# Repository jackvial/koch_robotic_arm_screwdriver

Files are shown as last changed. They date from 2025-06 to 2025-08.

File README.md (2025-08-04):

# Koch Robotic Arm Screwdriver

A screwdriver attachment and camera mount for the Koch robotic arm.

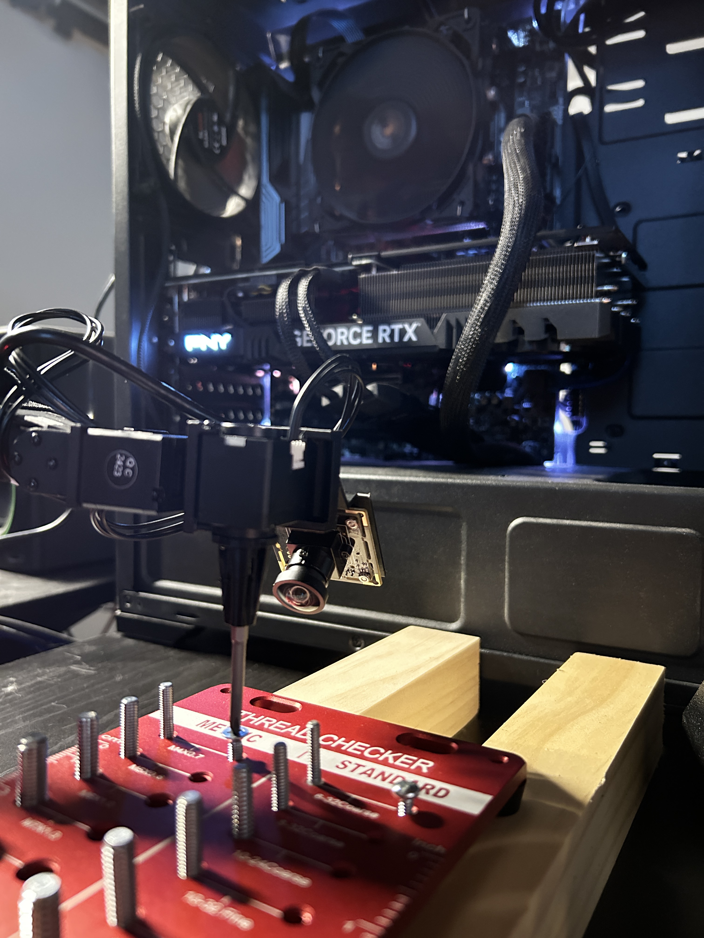
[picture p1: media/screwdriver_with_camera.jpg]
Screwdriver with camera


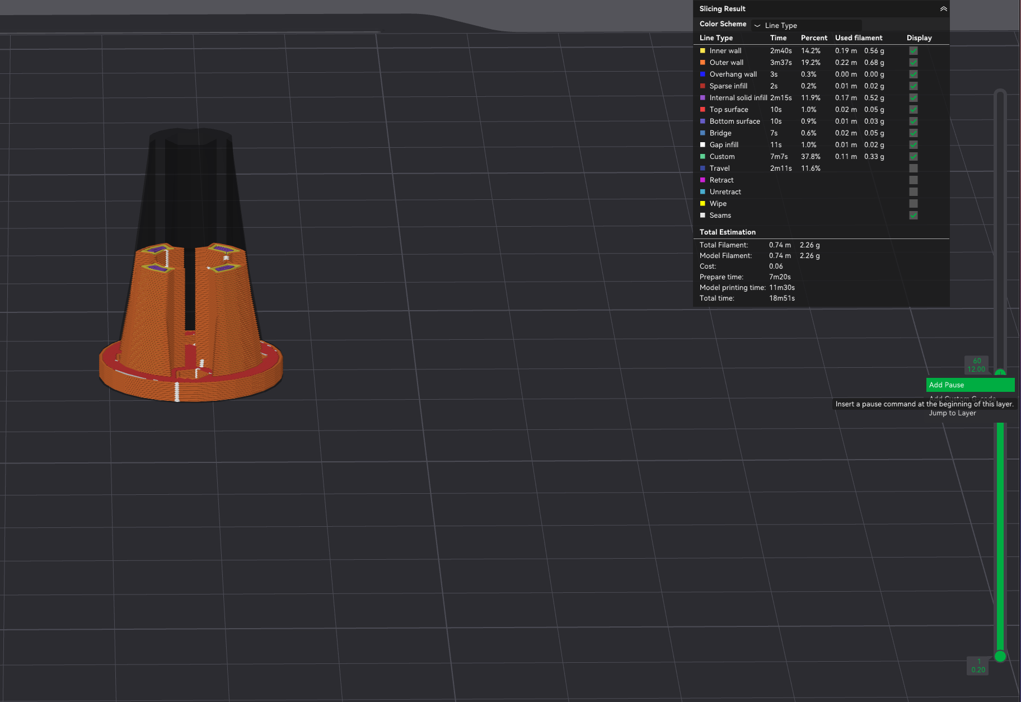
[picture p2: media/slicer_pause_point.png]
Slicer pause point


## Video Demo
[Watch the demo on YouTube](https://www.youtube.com/shorts/0c0qmF34xng)

## Screwdriver Bill of Materials
* SVPRO 5MP 30FPS USB Camera 
    * $53.99 on [Amazon](https://www.amazon.com/dp/B0D8SS2KNZ?ref_=ppx_hzod_image_dt_b_fed_asin_title_0_0&th=1)
* 6 mm diameter × 2 mm height neodymium magnets — 5 pcs  
    * $5.99 for 50 on [Amazon](https://www.amazon.com/dp/B079FLRQJP?ref=ppx_yo2ov_dt_b_fed_asin_title&th=1)*
* M2 8mm screws - I used this set
    * [Amazon](https://a.co/d/1YjSOn4)
* Precision screwdriver with standard 4mm hex shank bits - I am using the bits from this screwdriver
    * [Amazon](https://a.co/d/cEVycXf)

## Screwdriver Instructions
1. Position both parts on the print bed:  
   • `stl/screwdriver_servo_holder_with_camera_mount_v1.2.stl`  
   • `stl/koch_screwdriver_chuck.stl`
2. In your slicer (e.g. Bamboo Studio for the X1-Carbon) add a pause at the top of the magnet cavity.  
   See this tutorial: https://www.youtube.com/watch?v=SBewgnA0Z2s
3. When the print pauses, insert a stack of 5 magnets into the cavity.
4. Resume printing.

## Test Bed Bill of Materials
- 3 M4 hex nuts. I used the ones from this set on [Amazon](https://www.amazon.com/dp/B0CNY3BSXX?ref_=ppx_hzod_title_dt_b_fed_asin_title_0_0)
- 1 M4 8mm height flat head philips screw

## Test Bed Instructions
1. Position both parts on the print bed:  
   • `stl/test_bed.stl`
2. In the slicer, add a pause at the top of the nut cavities
3. When the print pauses, insert the 3 M4 hex nuts into the nut cavities.
4. Resume printing.

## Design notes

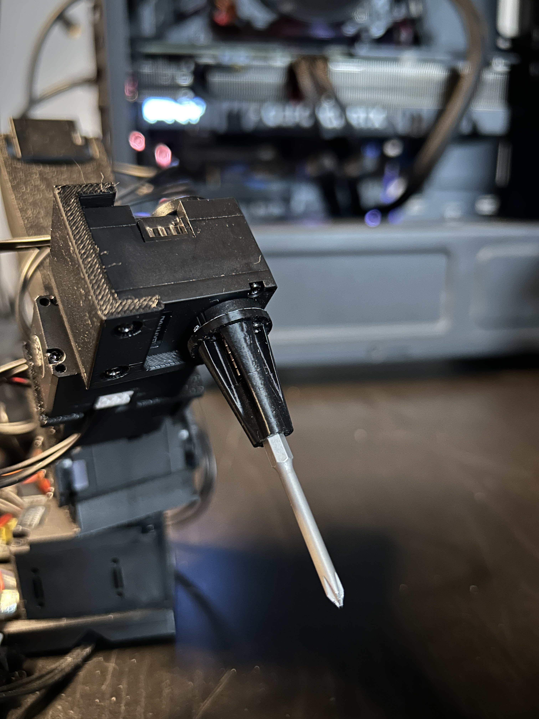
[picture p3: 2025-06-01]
media/koch_with_screwdriver.jpg

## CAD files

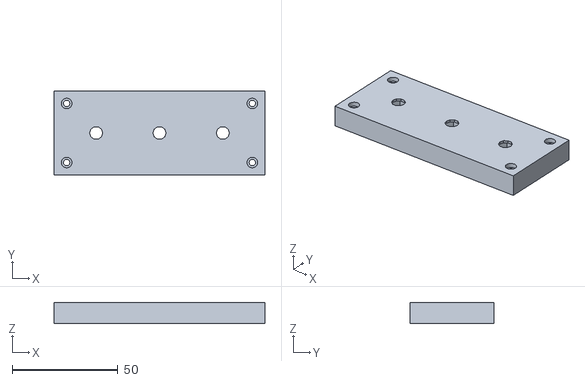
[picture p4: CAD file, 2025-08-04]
stl/test_bed.stl
100.0 x 40.0 x 10.0

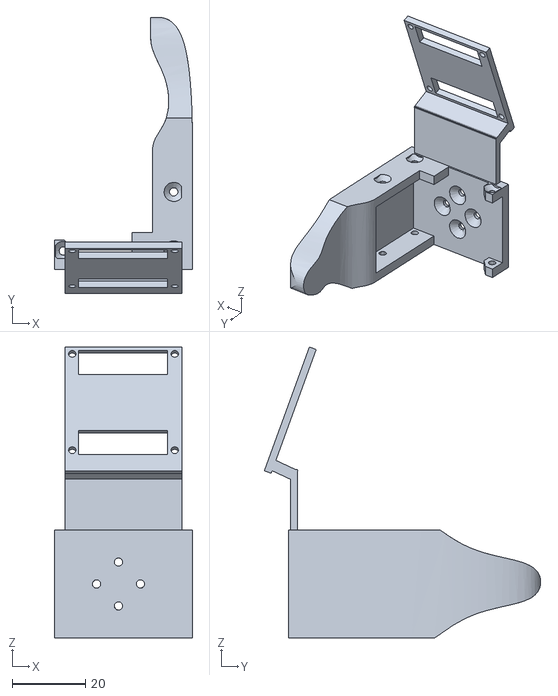
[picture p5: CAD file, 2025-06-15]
stl/koch_mount2.stl
37.8 x 75.5 x 79.5

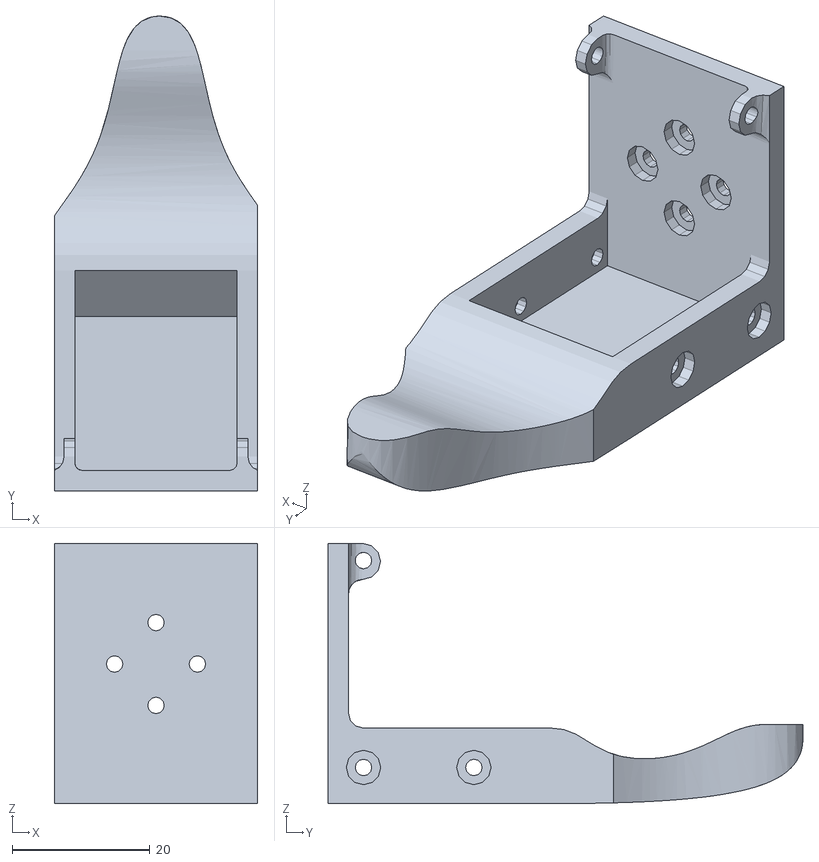
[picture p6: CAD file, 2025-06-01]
stl/Follower_Gripper_Static_Part.STL
29.5 x 68.9 x 37.8

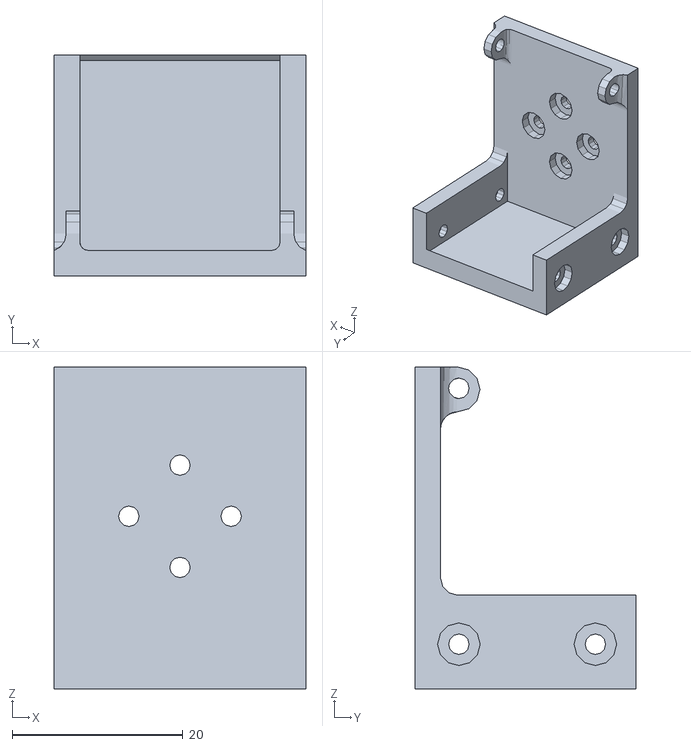
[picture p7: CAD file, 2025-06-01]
stl/modified_follower_gripper_static.stl
29.5 x 25.9 x 37.8

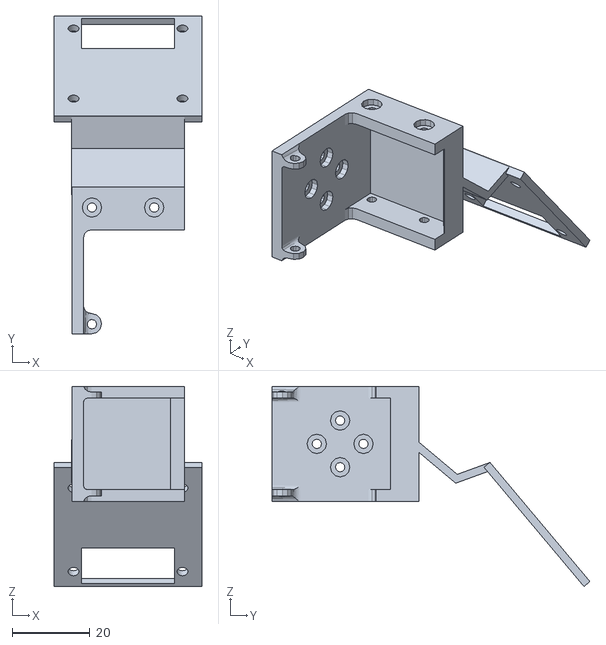
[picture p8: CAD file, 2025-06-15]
stl/screwdriver_servo_holder_with_camera_mount_v1.2.stl
38.0 x 81.7 x 51.4

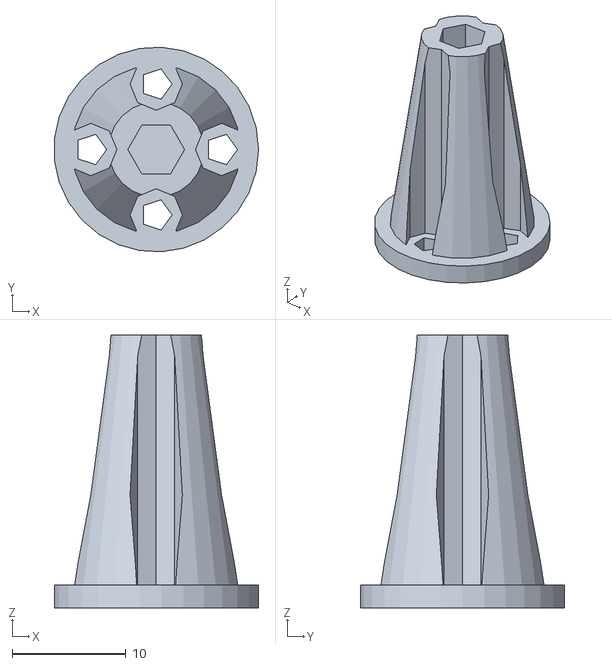
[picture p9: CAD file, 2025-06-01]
stl/koch_screwdriver_chuck.stl
17.9 x 18.0 x 24.0

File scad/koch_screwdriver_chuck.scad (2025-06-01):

plate_radius = 9;
plate_thickness = 2;
chuck_height = 22;
chuck_radius = 4.2;
chuck_base_radius = 7.4;  // Wider base for the cone
screw_hole_radius = 1.4;
screw_hole_offset = 5.75;
top_cylinder_height = chuck_height + 2;  // Height of cylinders above screw holes
top_cylinder_radius = 2.3;  // Radius of cylinders above screw holes

module solid_parts() {
    // Chuck plate
    cylinder(h=plate_thickness, r=plate_radius);
    
    // Chuck shaft
    translate([0, 0, plate_thickness]) {    
        cylinder(h=chuck_height, r1=chuck_base_radius, r2=chuck_radius);
    }
}

module plat_screw_hole() {
    cylinder(h=plate_thickness + 2, r=screw_hole_radius);
}

module magnet_cavity() {
    cylinder(h=10, r=3.4);
}

difference() {
    solid_parts();
    
    translate([0, 0, plate_thickness]) {
        cylinder(h=chuck_height + 1, r=2.5, $fn=6);
    }
    
    // Screw holes with cylinders above them
    translate([0, screw_hole_offset, -1]) {
        plat_screw_hole();
    }
    translate([0, screw_hole_offset, plate_thickness]) {
        cylinder(h=top_cylinder_height, r=top_cylinder_radius);
    }
    
    translate([0, -screw_hole_offset, -1]) {
        plat_screw_hole();
    }
    translate([0, -screw_hole_offset, plate_thickness]) {
        cylinder(h=top_cylinder_height, r=top_cylinder_radius);
    }
    
    translate([screw_hole_offset, 0, -1]) {
        plat_screw_hole();
    }
    translate([screw_hole_offset, 0, plate_thickness]) {
        cylinder(h=top_cylinder_height, r=top_cylinder_radius);
    }
    
    translate([-screw_hole_offset, 0, -1]) {
        plat_screw_hole();
    }
    translate([-screw_hole_offset, 0, plate_thickness]) {
        cylinder(h=top_cylinder_height, r=top_cylinder_radius);
    }
    
    translate([0, 0, plate_thickness]) {
        magnet_cavity();
    } 
}

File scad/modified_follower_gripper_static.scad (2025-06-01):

// Koch gripper with the claw lobbed off
translate([0, 0, 1]) {
    difference() {
        translate([-230, 0, 37]) {
            import("../stl/Follower_Gripper_Static_Part.STL");
        }
       
        translate([-33, -43, -15]) {
            cube([50, 50, 50]);
        }
   }
}

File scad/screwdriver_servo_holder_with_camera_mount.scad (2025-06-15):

// ========================= Parameters =========================
plate_thickness = 2;                // thickness of all small plates
screw_r         = 1.4;              // radius for M2.5 screw holes
mount_angle_1   = 50;               // first camera bracket angle (deg)
mount_angle_2   = 110;              // second camera bracket angle (deg)
mount_angle_3   = 40;               // third camera bracket angle (deg) 
socket_cut_size = [12, 24, 4];       // cut-out that clears the flat cable socket
cube_cut_size   = [50, 50, 50];     // large cube used to lob off the claw
cube_cut_pos    = [-33, 10, -15];   // position of cube_cut
follower_offset = [-222, 50, 37];   // translation for imported STL
mount_origin    = [-2, -19, 0];     // where the camera mount attaches
mount_plate_size = [40, 38, plate_thickness];
gusset_size     = 8;                // side length of the strengthening gussets
gusset_height   = 10;               // height of the corner gussets
// screw-hole pattern (XY translation); Z comes from each element's third value
screw_pattern = [
    [7,  5, -1],
    [7, 33, -1],
    [35, 5, -1],
    [35, 33, -1]
];

$fn        = 64;    // global smoothness for all circular geometry
$fn_screws = 32;    // finer tessellation for small screw holes
$render_vitamines = false;

// ========================= Utility Modules =========================

module plate(size) {
    cube(size, center = false);
}
module screw_hole(h, r = screw_r) {
    cylinder(h = h, r = r, $fn = $fn_screws);
}

module socket_cut() {
    cube(socket_cut_size, center = false);
}

module follower_gripper() {
    import("../stl/Follower_Gripper_Static_Part.STL");
}

// ========================= Assemblies =========================
module mounting_plate() {
    difference() {
        plate(mount_plate_size);
        // socket clearance
        // translate([2, 7, -1]) {
        //     socket_cut();
        // }
        
        translate([27, 7, -1]) {
            socket_cut();
        }
        // screw holes in the four corners
        for (p = screw_pattern) translate(p) screw_hole(plate_thickness + 2);
    }
}

module camera_mount() {
    // first small plate
    rotate([0, mount_angle_1, 0]) plate([15, 29, plate_thickness]);

    // The rest of the mount is transformed together, preserving the original nesting.
    translate([9.3, 0, -9.5]) {
        // second small plate
        rotate([0, mount_angle_2, 0])
            plate([10, 29, plate_thickness]);

        // main mounting plate with holes and socket cut
        translate([-3.5, -4.5, -9.5])
            rotate([0, mount_angle_3, 0]) {
                mounting_plate();
                
                // Camera line of sight
                if ($render_vitamines) {
                    translate([(mount_plate_size[0] / 2) + plate_thickness, (mount_plate_size[1] / 2), 0]) {
                        cylinder(h = 100, r = 1.4);
                    }
                }
            }
    }
}

// ========================= Top-level Model =========================
rotate([90, 90, 0]) {
    
    // Drill bit to align the camera mount
    if ($render_vitamines) {
        translate([70, -5, 26]) {
            rotate([0, -90, 0]) {
                cylinder(h = 57, r = 1);
            }
        }
    }
    
    difference() {
        // imported follower gripper body
        translate(follower_offset) { 
            follower_gripper();
        }

        // cube used to remove claw section
        translate(cube_cut_pos) { 
            cube(cube_cut_size, center = false); 
        }
    }

    // camera mount assembly
    translate(mount_origin) camera_mount();
}

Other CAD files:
scad/test_bed.scad

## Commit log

2025-06-01 Added readme
    [Follower_Gripper_Static_Part.STL, koch_screwdriver_chuck.scad, koch_screwdriver_chuck.stl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]
2025-06-15 Added camera mount
    [koch_mount2.stl, screwdriver_servo_holder_with_camera_mount.scad, screwdriver_servo_holder_with_camera_mount_v1.2.stl]
2025-06-22 Add camera to BOM
2025-07-25 updated bom
2025-08-04 Added test bed and updated readme
    [test_bed.scad, test_bed.stl]
